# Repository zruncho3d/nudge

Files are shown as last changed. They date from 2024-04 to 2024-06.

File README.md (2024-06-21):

## Nudge - automatic nozzle alignment, made easy

*One microstep for a probe.  One giant leap for multiple-head-kind.*

**tl;dr:** Manual calibration sucks, but with this probe, you can get fresh, fully-automatic offset alignment on every print.

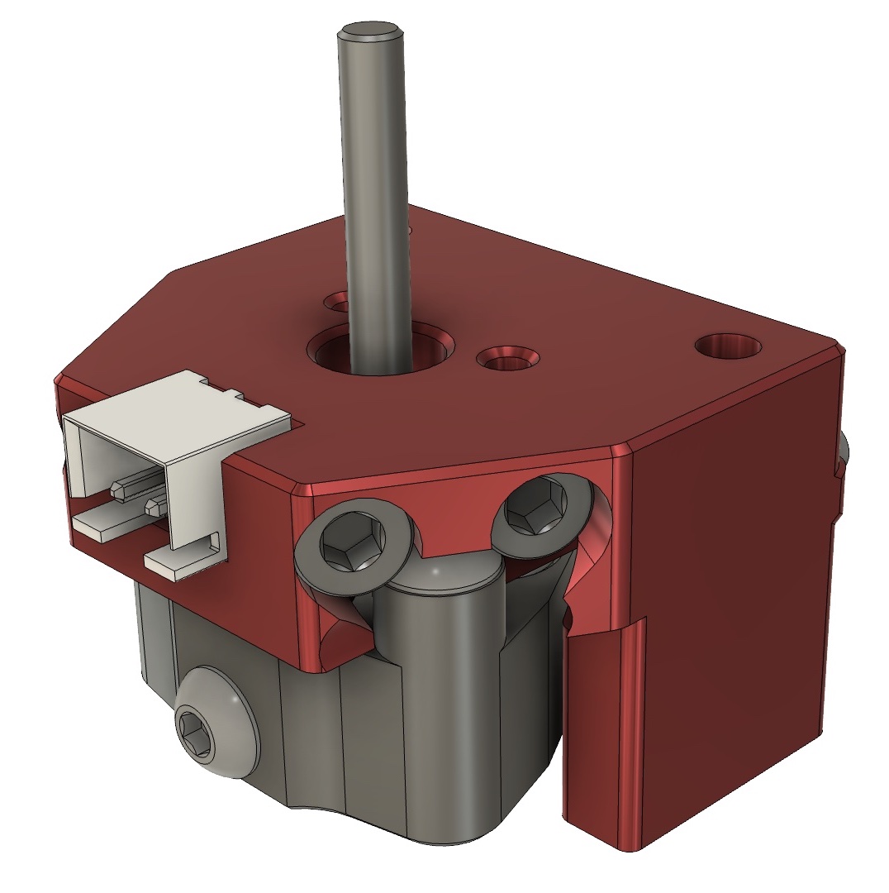
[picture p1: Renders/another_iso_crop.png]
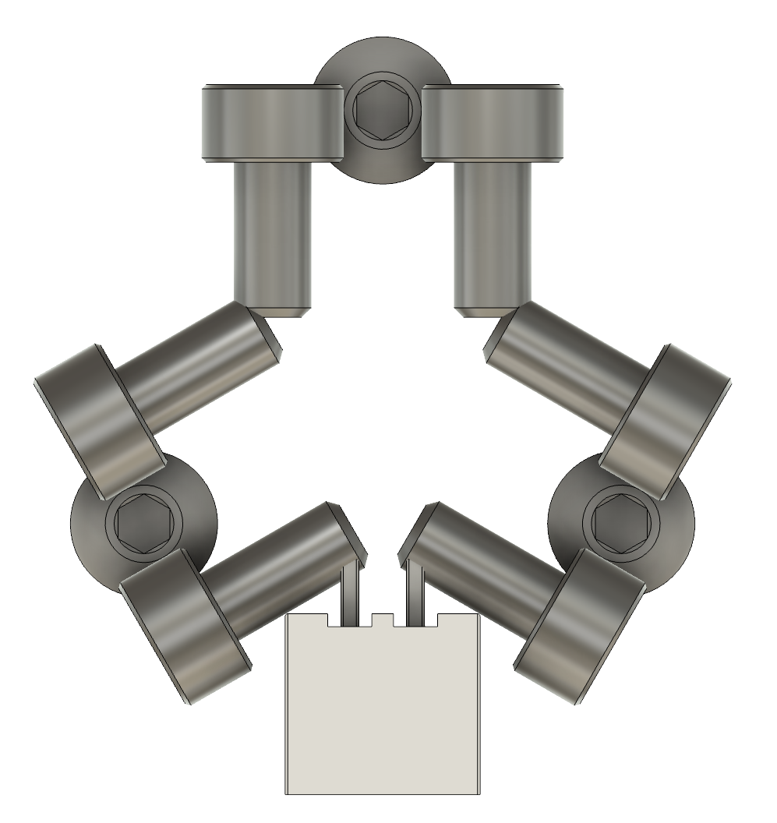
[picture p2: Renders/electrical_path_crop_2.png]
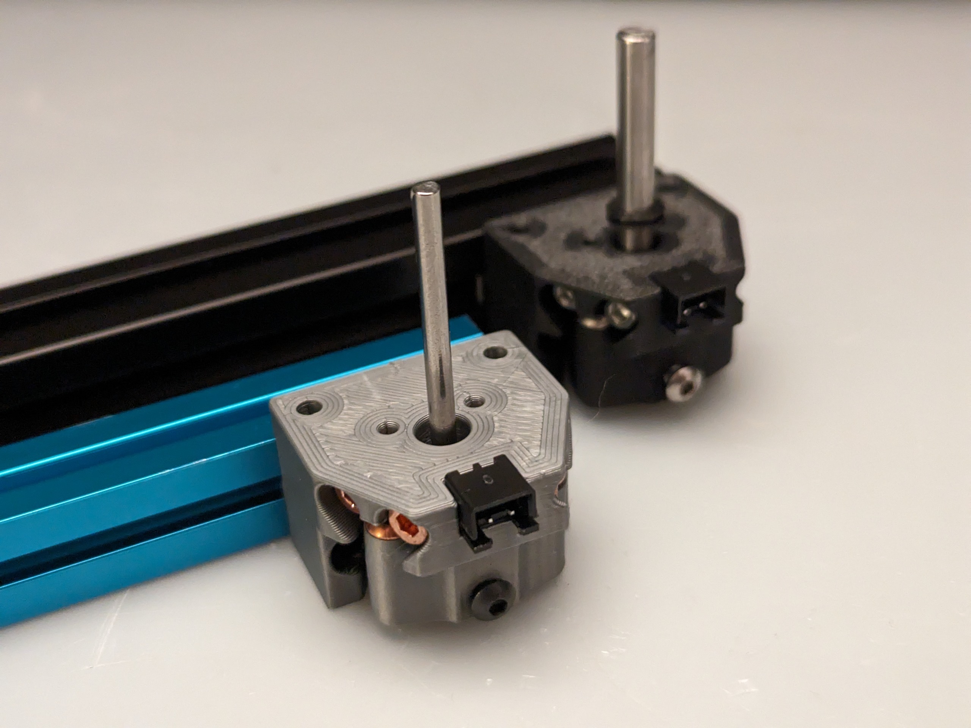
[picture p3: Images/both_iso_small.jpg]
|  |  |  |
| - | - | - |

## Nudge in action! >>>  

**Nudge** is a low-cost, high-repeatability probe to enable automatic nozzle alignment on multi-toolhead 3D printers (IDEX, Dual Gantry, and Toolchanger).  

It’s like a Z endstop, but can be nudged in X and Y directions, too.  

When the metal probe tip is nudged by the nozzle, a button-head screw in the Wobbler lifts off slightly from the smooth socket-head screws in the Mount, breaking the electrical path.  Software nudges the nozzle against the probe in Z, then X, and Y, repeating this process to determine offsets between any number of toolheads.

When multiple heads can work together, with perfect alignment, multi-color and multi-material prints look great!  

Here's a sample from Ankurv ([3DUnplugged]()), whose [Daksh v2]() toolchanger uses Nudge to ensure alignment betweeen heads:

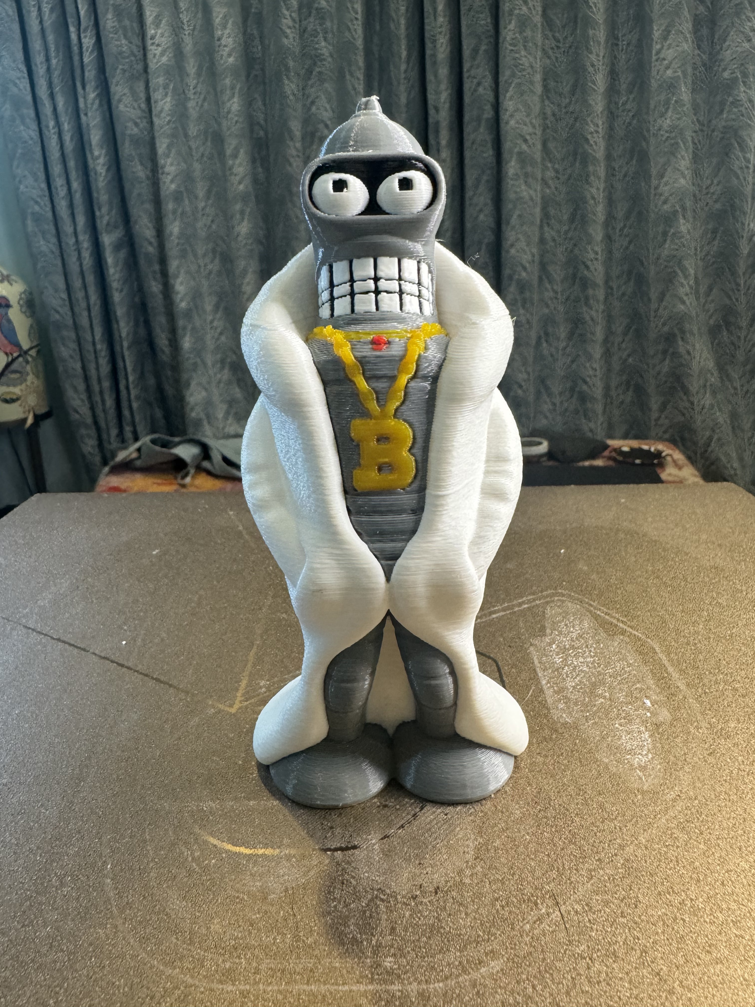
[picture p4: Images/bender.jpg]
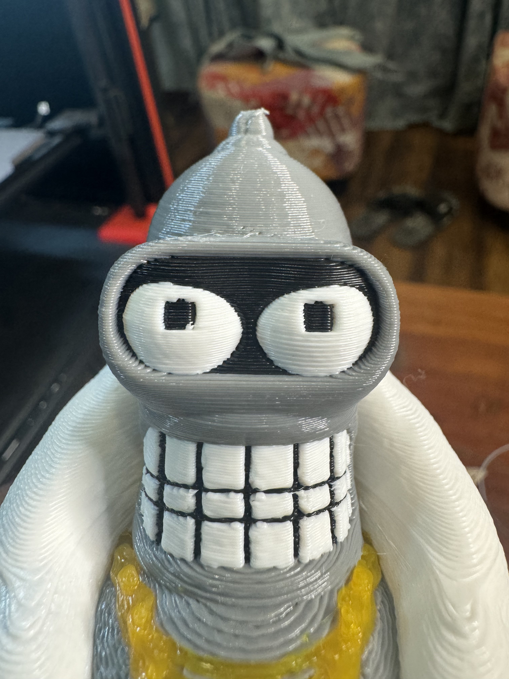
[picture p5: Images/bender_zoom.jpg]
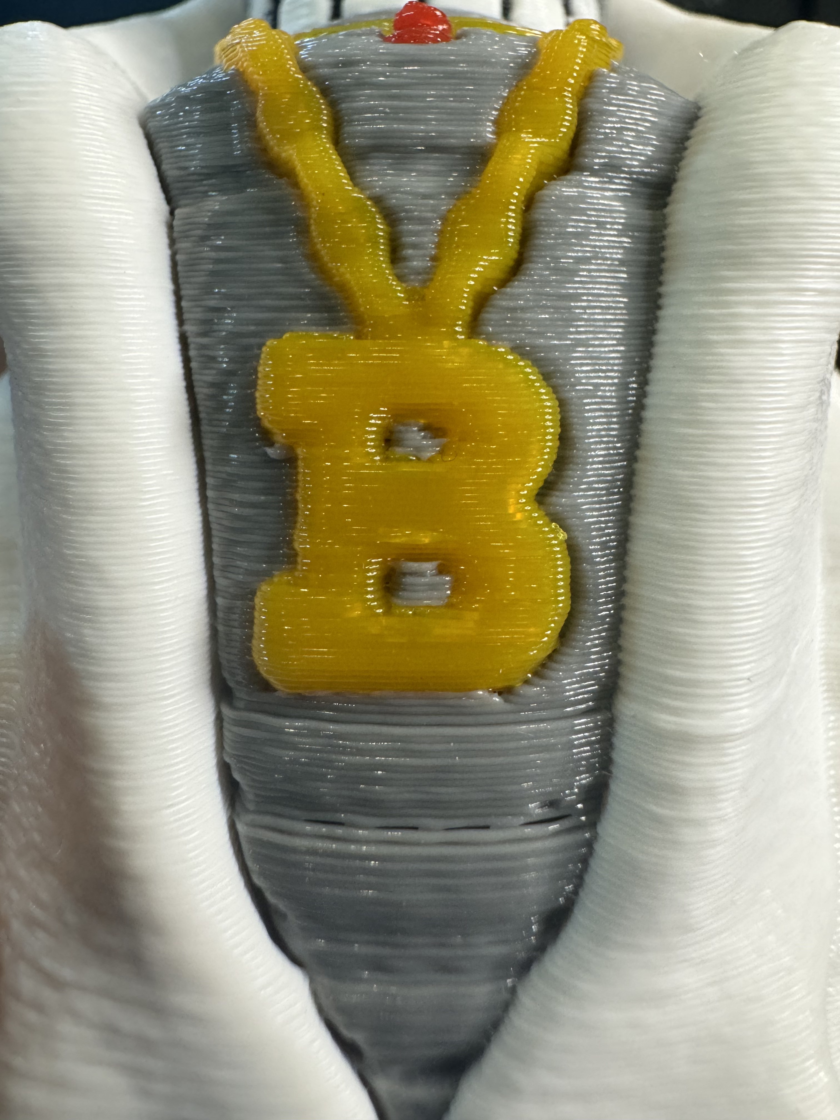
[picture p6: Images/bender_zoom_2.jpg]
|  |  |  |
| - | - | - |

Here's a sample from Zruncho of some Voron cubes.  The full-size cube would have been perfectly aligned if the nozzle was cleaned first!

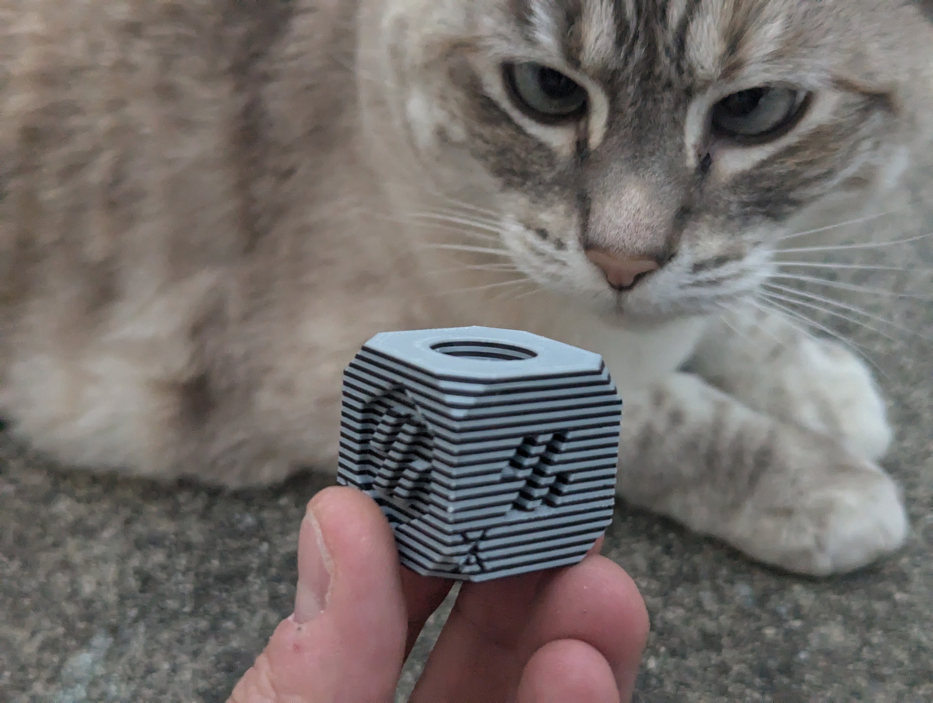
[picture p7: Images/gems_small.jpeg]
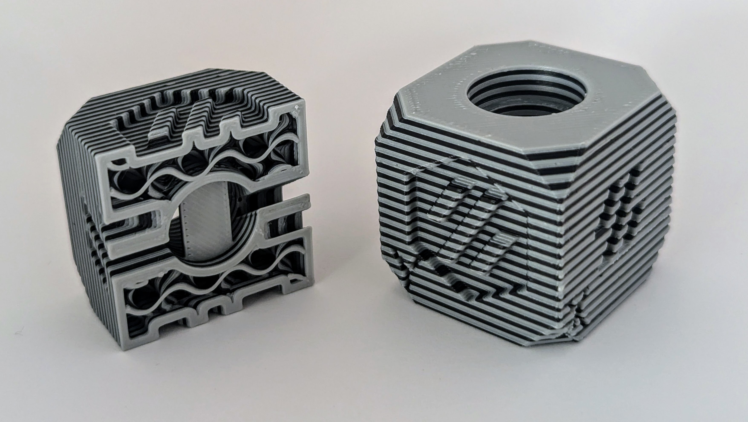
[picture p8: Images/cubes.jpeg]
|  |  |
| - | - |

You can print, build, and deploy a Nudge in as little as one hour, with only $10 in parts:

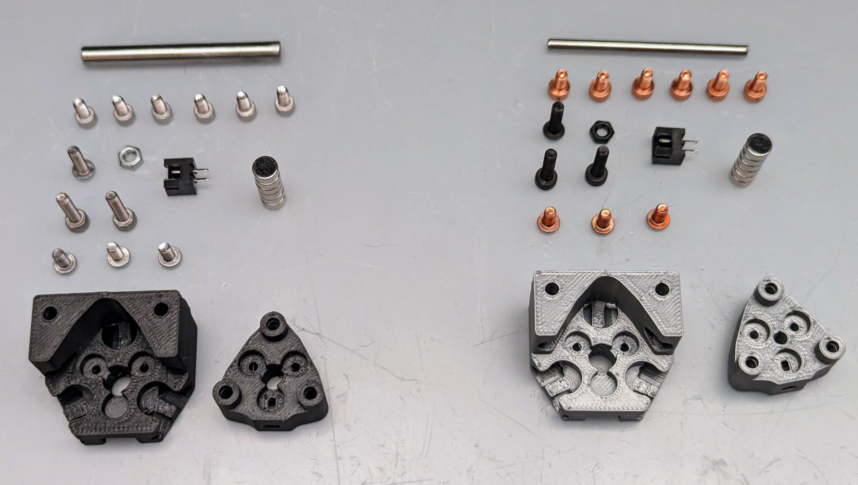
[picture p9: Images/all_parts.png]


Build it using the instructions in this repo, or with [this video]((https://youtu.be/6eRomxUo7TI).  Yes, it used to have a 'y' at the end of the name.  Note also that this video is slightly out of date - for example, now, Nudge has a straight-through JST, rather than a right-angle JST, and plastic to ensure the horizontal screws stay aligned.

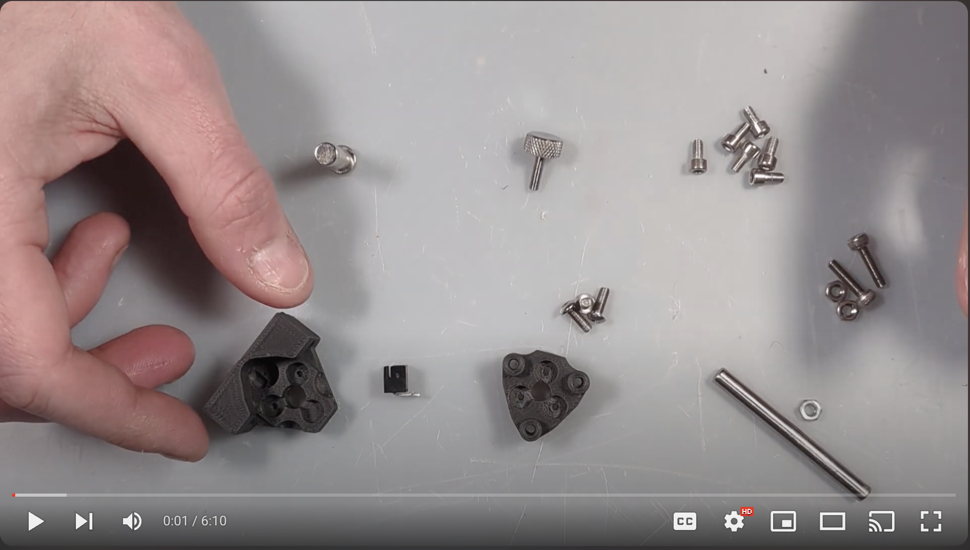
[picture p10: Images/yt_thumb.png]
(https://youtu.be/6eRomxUo7TI)


## [> > > Watch build](https://youtu.be/6eRomxUo7TI)

Nudge is highly repeatable; here's an early sample of probing accuracy from a 10-sample run:
```
Printing stats for x:
  Range: 0.0023
  Standard Deviation: 0.0010
Printing stats for y:
  Range: 0.0016
  Standard Deviation: 0.0007
--- 95.45 seconds total; 19.09 per iteration ---
```

Definitely usable!  Z is not quite as good, though, so you may still want to keep that endstop switch around for determining Z offsets.

**Firmware Support**: Nudge works great on CoreXY with nozzle alignment code from [Viesturz' klipper-toolchanger](https://github.com/viesturz/klipper-toolchanger) repo, but other kinematics should be possible with Klipper tweaks.

| Printer Type | Klipper Kinematics type | Test/Support Status |
| - | - | - |
| Toolchanger | CoreXY | :white_check_mark: |
| IDEX | Hybrid CoreXY w/ Dual Carriage | :white_check_mark: (as of 2024-06-19) |
| IDEX | CoreXZ Dual Carriage | :x: Fails during probing |
| DG | Dual Gantry CoreXY | :x: Fails during probing |

Related patches:
* [RCF's klipper-toolchanger fix for IDEX](https://github.com/viesturz/klipper-toolchanger/pull/23/commits)
* [Frans-Willem's Klipper PR for IDEX](https://github.com/Klipper3d/klipper/pull/6486)

No, fully-automatic offsets are not yet supported.  If you figure this out, please share.

**Hardware Support**: Mounting options for many common multi-toolhead open-source printers/mods are included here, including Trident, Tridex, Tri-Zero, Double Dragon, Dueling Zero, V2, Micron, F-Zero, and more.  One almost certainly fits!  *Unlike other options, a Nudge can be permanently mounted within a hot chamber, with as little as 6mm overtravel.*

**Parts to print**:

| Mount | Wobbler | Floating Base (optional) | Indexed Base (optional)  |
| - | - | - | - |
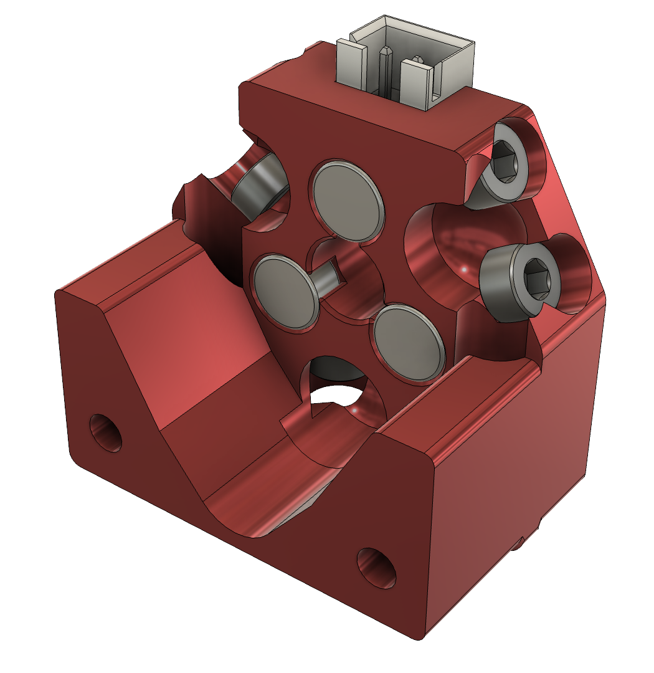
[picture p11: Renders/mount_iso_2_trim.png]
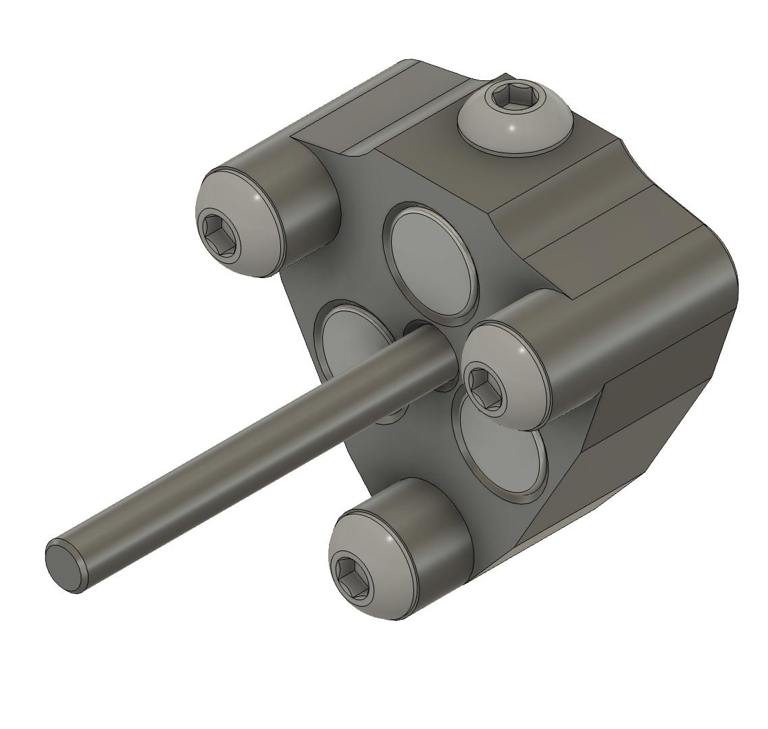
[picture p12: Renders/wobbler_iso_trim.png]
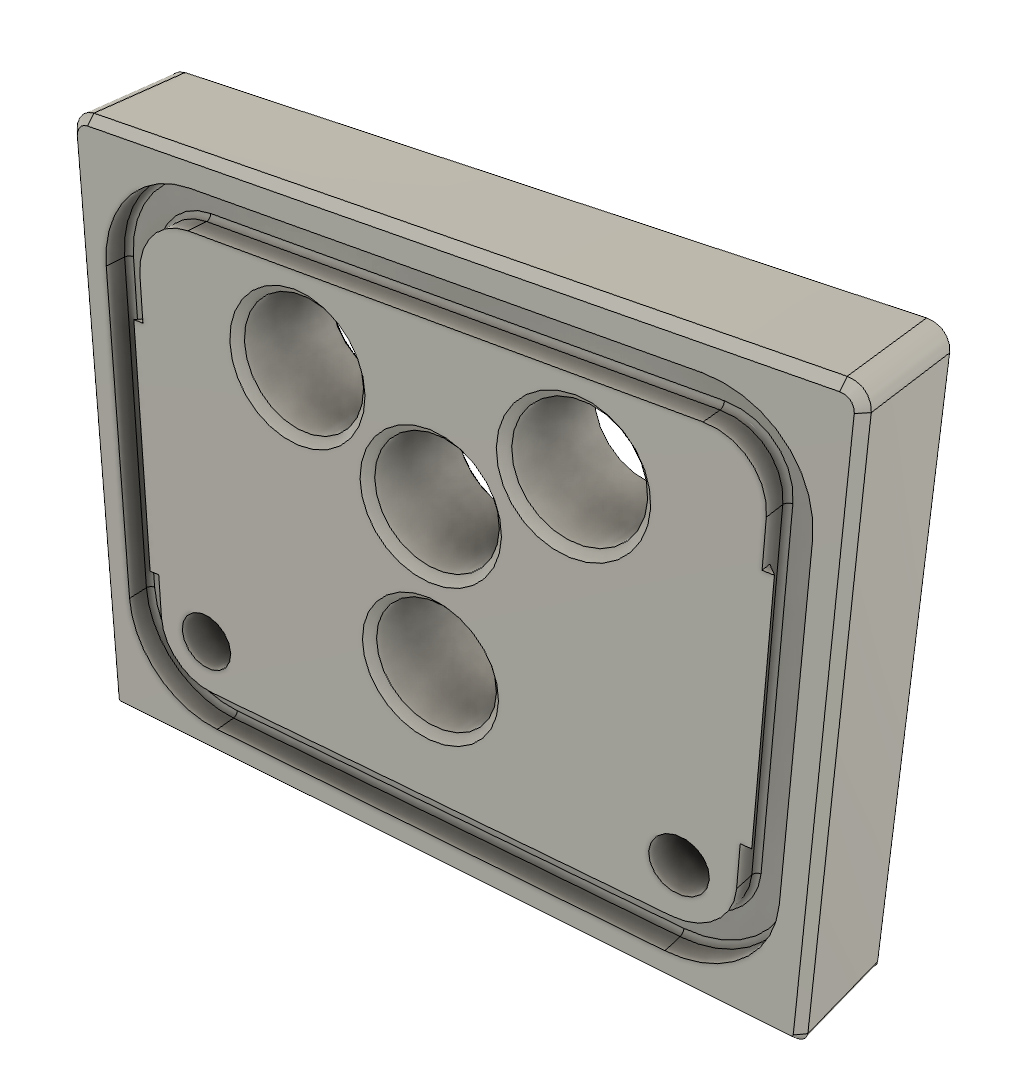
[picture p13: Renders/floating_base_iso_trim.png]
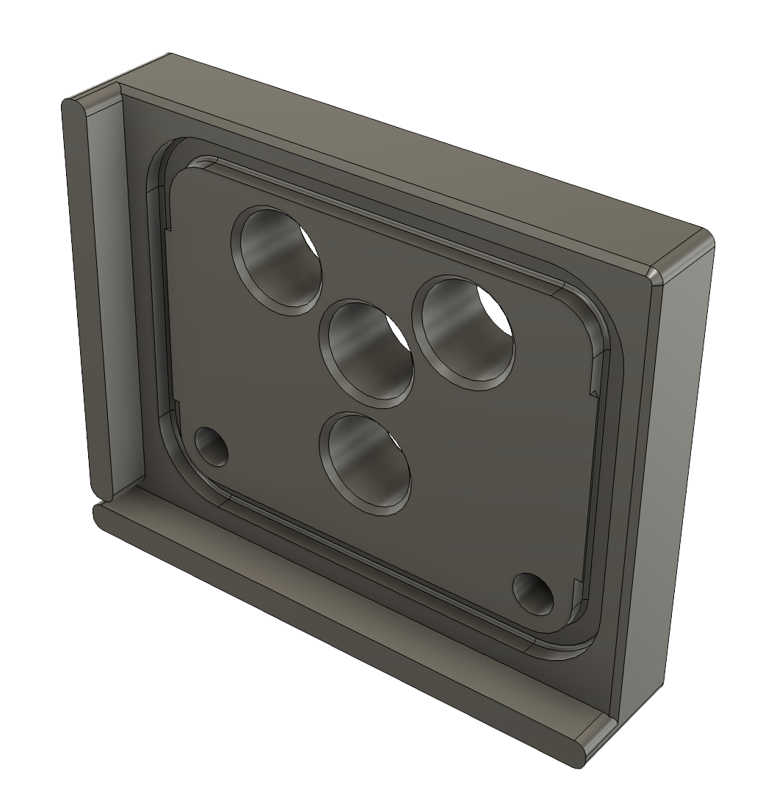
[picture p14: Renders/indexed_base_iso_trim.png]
|  |  |  |  |

**Mount options:**

| 2020 | 1515 High (sticks up) | 1515 Low (sits low) |
| --- | --- | --- |
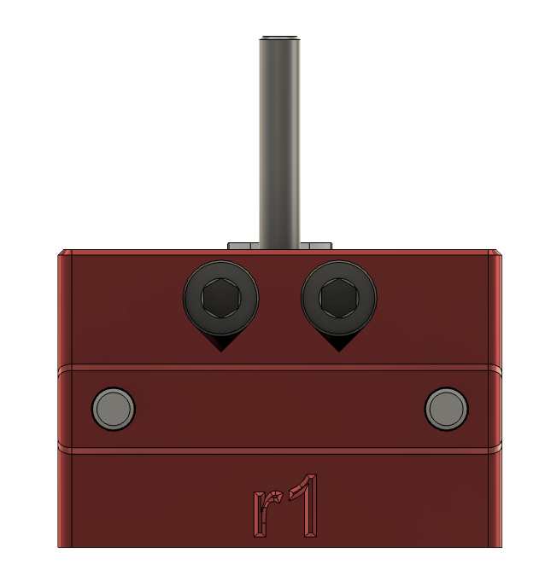
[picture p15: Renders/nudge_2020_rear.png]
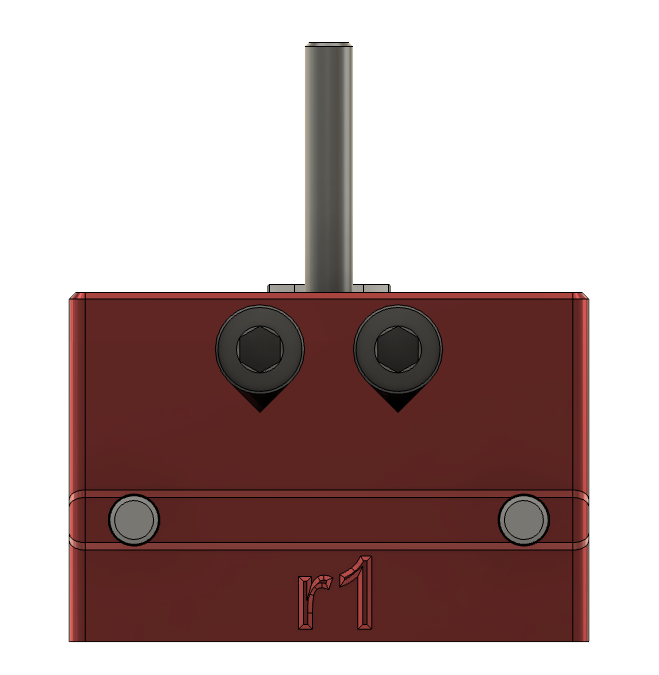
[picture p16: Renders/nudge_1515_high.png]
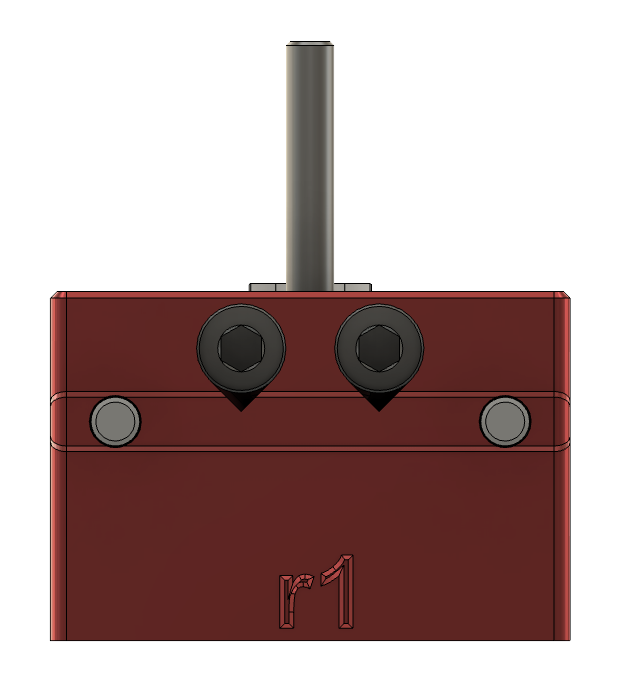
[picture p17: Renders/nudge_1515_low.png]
|  |   |  |

**Wobbler options**: 3mm Pin, 5mm Pin, or M3 screw and internally-threaded dowel:
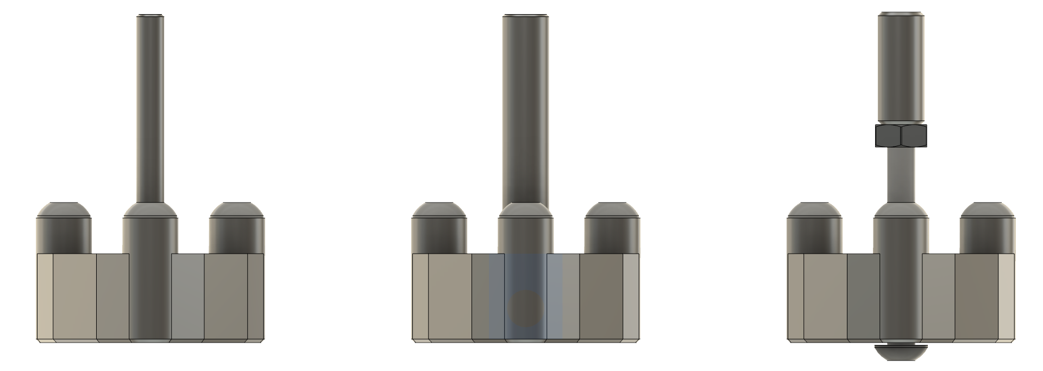
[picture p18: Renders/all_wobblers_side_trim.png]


**Sound good?**  Jump to the [Instructions](INSTRUCTIONS.md) section to get started and find the printed parts to match your printer's layout; one should fit!  

Or, read about some advantages to this design...
## Advantages
 * **Highly repeatable** - single-microstep-level repeatability (typically below .003125 Std Dev over 10 samples).
 * **Low cost** - approximately $10.
 * **Easily sourced** - Zruncho had all parts on hand already. All are on Amazon and AliExpress; smooth M3x6 SHCS is the only “new” part.
 * **Minimizes travel loss** - probe tip fits next to the bed; as little as 6mm overtravel suffices.
 * **Easily adjusted** - Z height, position along an extrusion, and magnet forces are all adjustable, in-situ.
 * **Fast build and print** - print, build, and test in about an hour.  No heatsets, soldering, or gluing required.
 * **Flexible mounting** - options are available to fit almost any printer.
 * **Simple wiring** - 2-pin JST header matches existing Z nozzle endstops.
 * **Temperature-tolerant** - no electronics to burn out at chamber temps (like a camera), and no plastic next to the bed to melt.
 * **In-place mounting option** - run this at the start of every print, just like a QGL or ZTA cycle, so that offsets are perfect, even with temperature changes, or after tightening or maintenance.

Like what you see?  [Buy me a coffee](https://ko-fi.com/zruncho3d) to show the love and enable future mods and content - stuff like [F0](https://github.com/zruncho3d/f-zero), [T0](https://github.com/zruncho3d/tri-zero), [B0](https://github.com/zruncho3d/boxzero), [X0](https://github.com/zruncho3d/double-dragon), [D0](https://github.com/zruncho3d/DuelingZero), [DX](https://github.com/zruncho3d/DuelingX), [ZeroPanels](https://github.com/zruncho3d/ZeroPanels), [ZeroClick](https://github.com/zruncho3d/zeroclick), [NoDropNuts](https://github.com/zruncho3d/f-zero/tree/main/STLs/NoDropNuts), [Poke](https://github.com/zruncho3d/poke), [Vampire Bat](https://github.com/zruncho3d/vampire_bat), and more.

 :heart: *-Zruncho*

## What's Here?

- #### [BOM](BOM.md): Parts list to build your own
- #### [Instructions](INSTRUCTIONS.md): Instructions to print and assemble
- #### [Configuration](CONFIGURATION.md): Configuration - firmware & macros
- #### [Design](DESIGN.md): Learn about why Nudge is designed like that!
- #### [FAQ](FAQ.md): Common questions, answered

## Troubleshooting

**Probe not returning to center?** Magnet force may be insufficient, especially with heavier 5mm pins.  You can easily increase magnet force by cutting the screw towers and aligning the BHCSes to decrease magnet distance.  You can also just push the magnets out slightly for the same effect.  Worst-case use stronger magnets.

**Probe triggered early?** Increase `spread`, improve the initial alignment accuracy, or add travel (by moving the bed or sensor).

**Probe triggering unreliably?** Check each pair of screws with a multimeter.  After a few heat cycles, you will probably need to tighten the SHCSes, as the plastic likes to relax a bit.

**High result variation?** Check the rigidity of the mount and be absolutely sure

**Unsatisfied with Z repeatability?** Z is just not as good, due to the design.  You can keep your original endstop and wire it inline with the original Z endstop, or you can flip the Nudge upside down and change the config to use Tap/Boop etc for the Z probing.

## Support

Find the thread in the User Projects forum channel on the [DoomCube Discord](https://discord.gg/doomcube) and post there.

## Credits

**Enjoy!** I hope you enjoy using this as much as the beta team did bringing this to release!  

Special thanks to `Caza` for critical design feedback and ideas, `Ankurv` for all-up testing,  and the beta team who helped validate the design: `Telxoid`, `Esoterical`, `SteveBuilds`, and others who provided data and feedback, including `RCF` and `Frans-Willem`, who created a PRs for IDEX.

We made a lot of prototypes and test articles to get here.

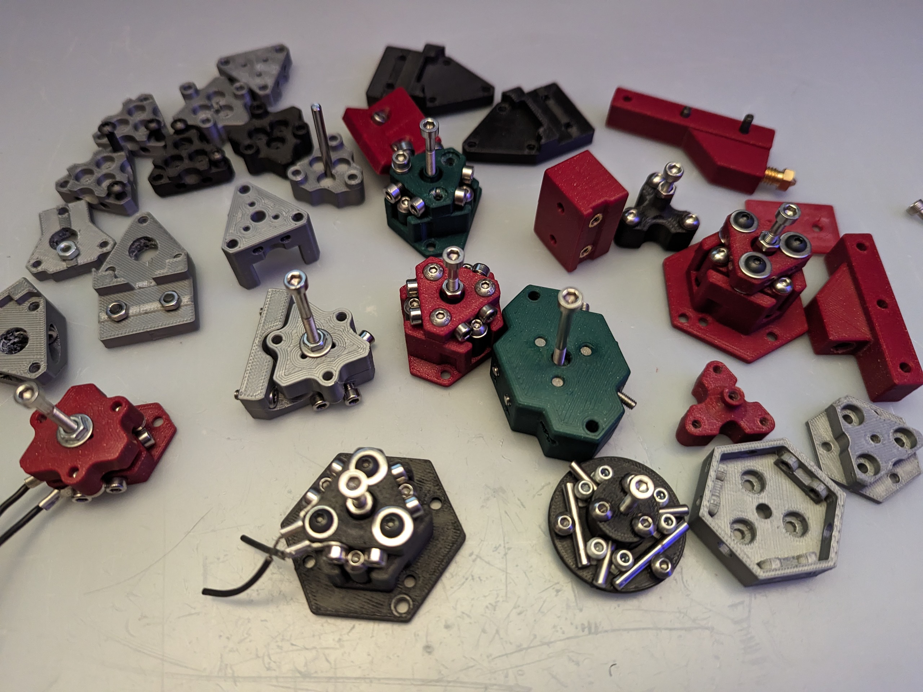
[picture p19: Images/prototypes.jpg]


It's 60+ and this isn't even all of them.

Thanks also to [Fabreeko](https://www.fabreeko.com/) for supporting this build!  Without HoneyBadger rails, the test gantry would not have happened, and Nudge would not have been as good.  Support vendors like this, which support open-source dev, whenever you can.

-Z

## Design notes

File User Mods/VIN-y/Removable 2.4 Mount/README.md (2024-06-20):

# About

This mod prove a repeatable mounting point for the stock Nudge near the back right corner of the 2.4 bed.

### Feature:

* Avoid reducing built volume in the Y-axis.

* Provide docking point for the Nudge, when not in usage.

* Feature a safety switch, that is triggered and prevent attempts to calibrate if the nudge is still docked.

### BOM:

* 3mm X 20mm pin (2 off)

* 6mm X 3mm, Neodymium Magnet (3 off)

* 3mm Bore x 5mm OD x 5mm Length Plain Bearings (6 off)

* Micro switch (1 off)

* 2mm self-tapping screws (2 off)

* M3 x 20mm (2 off)

* M3 x 18mm (1 off)

* M3 x 5 x 4 threaded insert (1 off)

* M3 washer (1 off)

* M3 x 25mm counter sunk (2 off)

* Super glue - for the magnets (optional)

### Notes:

* As the 3mm pins and sleeves are press-in-place, you might need a parallel clamp that can open at least 32mm wide. Alternatively, you can widen the holes with 3mm and 5mm drill bits.

* BE MINDFUL OF THE MAGNET DIRECTION. The part will need to be destroyed for magnet recovery.

### Pictures:

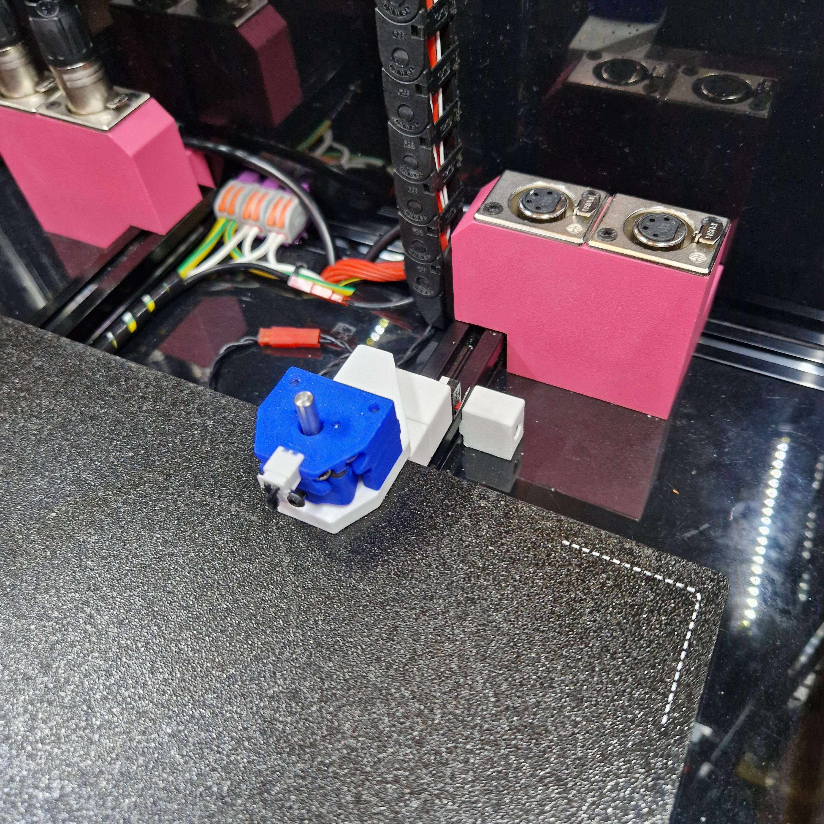
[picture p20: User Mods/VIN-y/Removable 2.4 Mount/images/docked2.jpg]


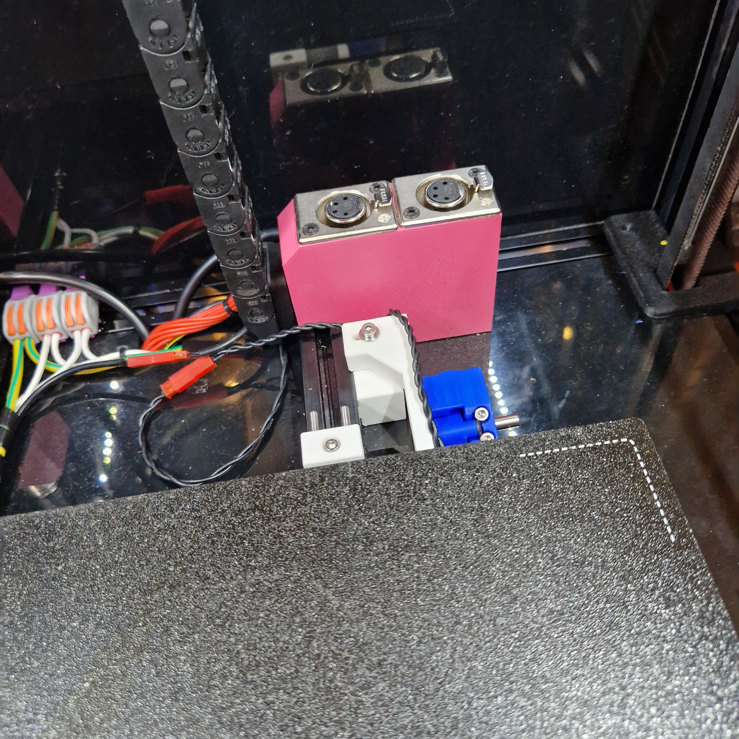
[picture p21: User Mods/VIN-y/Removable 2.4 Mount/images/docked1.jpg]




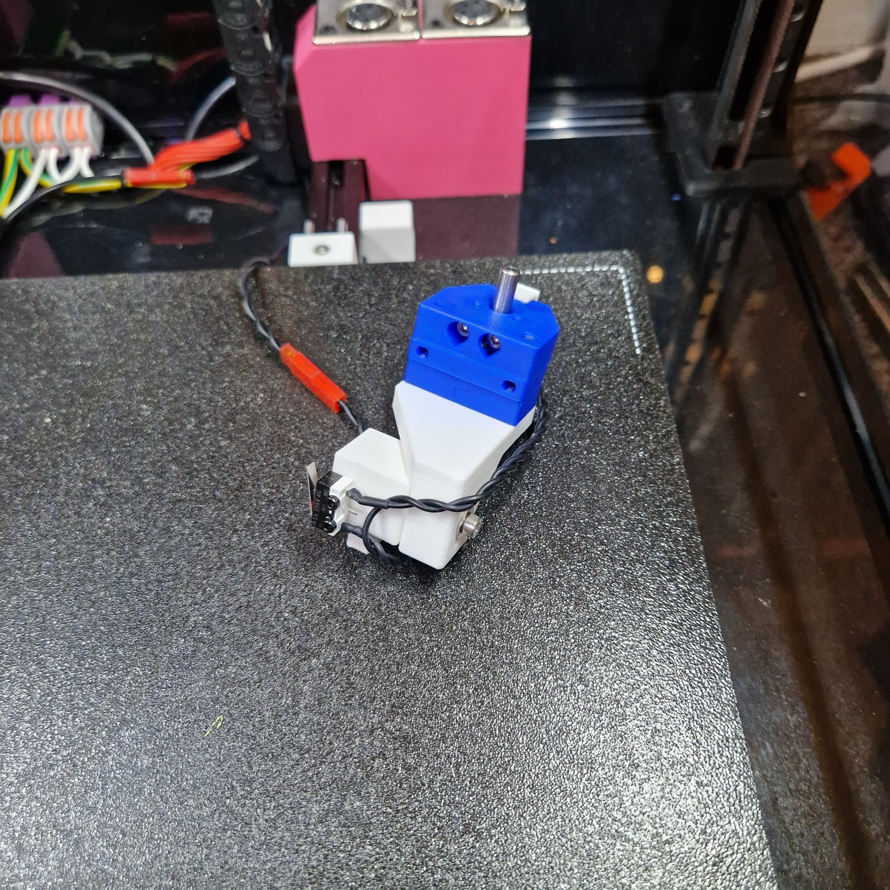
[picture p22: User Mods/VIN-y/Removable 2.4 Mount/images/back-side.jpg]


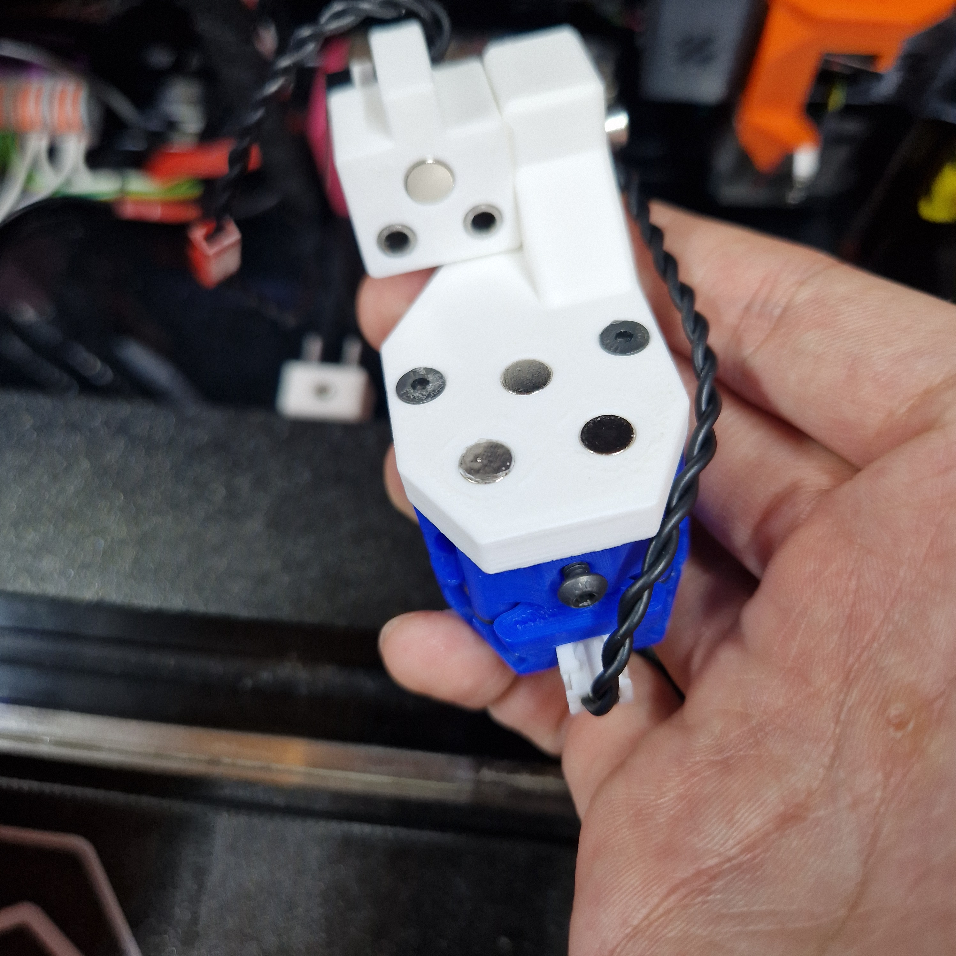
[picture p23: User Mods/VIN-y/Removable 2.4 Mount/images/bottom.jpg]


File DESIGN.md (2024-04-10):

# Design

**What’s interesting here?**

There's a lot of design complexity in a tiny space.  This is a 100% functionality-optimized design.

The key is the electrical layout.

In Nudge, M3 socket-head screws serve triple-duty as (1) NC (normally-closed) electrical contacts, (2) Maxwell-type kinematic couplings, and (3) contacts for the external (JST) connection.  Let's unpack that.

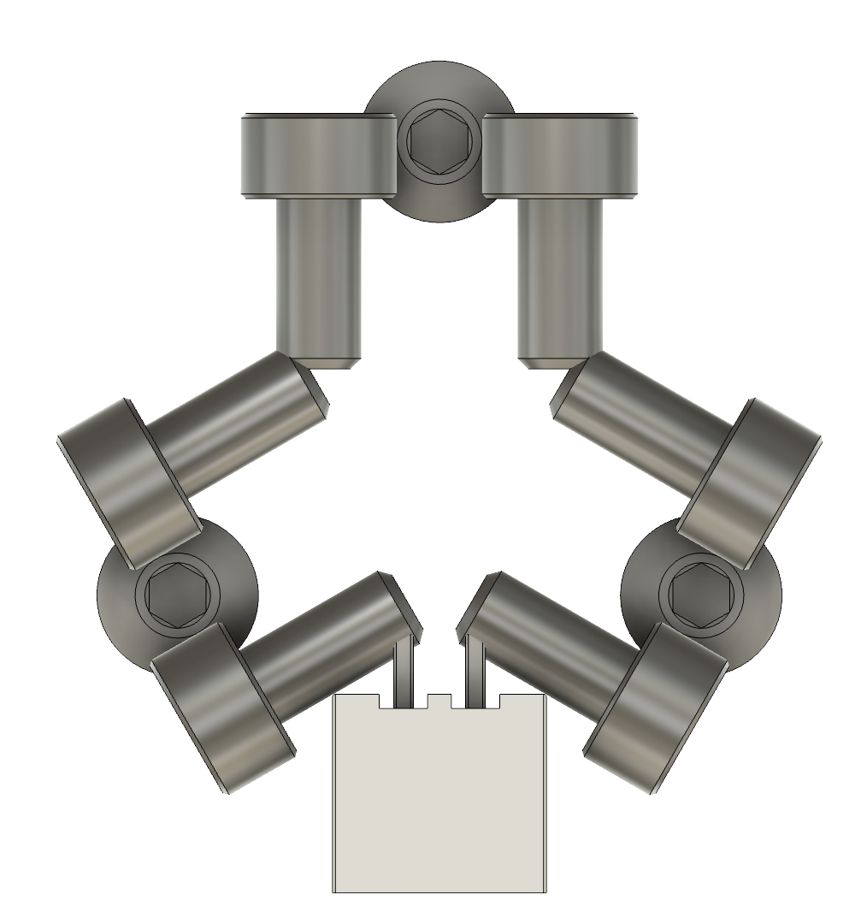
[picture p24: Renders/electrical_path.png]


**Electrical Contacts**: the cylindrical surface of the socket-head screws interacts smoothly with M3 button-head screws and forms a good electrical contact when pushed together with enough force.  Basic N35 6mm magnets work well here; in tests, this setup proved more repeatable than springs, without requiring any force tuning.  You can still tune the attraction between the mount and the wobbler, by unscrewing the wobbler screws evenly.  Stronger magnets required too much probe force, which measurably stretched the belts during long repeatability tests.

The screw tips press into each other, closing electrical contacts; this choice eliminated the need for more parts.  Originally, the screws faced out and used carefully bent solid wires or ring/spade terminals with flexible wire.  Screws facing in is much better.   Thanks `caza` for that suggestion!

Putting both parts of the SHCS to work required designing around specific screw lengths, and getting it all to work with tiny M3x6 screws was a challenge.

**Maxwell-type Kinematic Coupling**: A Maxwell coupling is a type of kinematic (repeatable) coupling that is symmetric.  The whole setup is similar to a Renishaw-style touch probe for CNC.

**Contacts for external JST connections**: the screw cuts a thread against the square JST terminals to close the connection.  The design evolved from ring terminals clamped by the screws (extra parts to source), to direct wire clamps, to a vertically-pointed straight JST, to a right-angle JST, to finally, a front-facing straight-through JST.  If people have issues with the cut screws, we can always revert to right-angle terminals.

**Design for Printability**:
A lot of thought/work went into designing this for clean 3D printing:
* overhangs beyond 45 degrees are avoided: teardrops around the rear-most two screw holes are an example
* careful multi-stage bridging near the JST connector
* the STls are oriented with seams at back

**Design for Assembly**:
* The shrouds around the SHCS guide screw in; without these features, the SHCS can go in slightly crooked.
* Magnet removal holes help when you have bajillions of prototypes
* Magnet holes are aligned to perimeters to enable press-fit magnets
* All formed threads have small counterbores to hold the screws ("easy starts)"
* The bases have little grips for the filament or o-ring.
* An earlier version required a separated mount and core, but these made sense to integrate, and Nudge became more compact and faster to assemble.
* Out of all the probe targets tried, pins were the fastest to assemble in the field, especially when combined with a locking screw.

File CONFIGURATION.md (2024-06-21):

# Configuration

Instructions below assume Klipper.  If you use RepRapFirmware or another firmware, PRs are welcome.

#### Add klipper-toolchanger code to Klipper

Formerly called NozzleAlign, the `tools_calibrate` code by Viesturz in the `klipper-toolchanger` repo finds the center of the probe, as well as computes the XYZ offsets relative to a different probing run.  CoreXY toolchangers have always been supported, and as of 2024-06-19 and a [patch by RCF](https://github.com/viesturz/klipper-toolchanger/pull/23/commits), IDEX support is merged into the mainline.

This code plunges to find the Z position, then moves in +X, -X, then -Y, +Y directions, with a Z offset you select.

These instructions come from Viersturz’ [klipper-toolchanger](https://github.com/viesturz/klipper-toolchanger) repo.

First, SSH to your Klipper system, then install the klipper-toolchanger code:
```
wget -O - https://raw.githubusercontent.com/viesturz/klipper-toolchanger/main/install.sh | bash
```
Klipper should restart without issue.

As best practice, enable easy updates: add this chunk to Moonraker.conf and restart Klipper when prompted:
```
[update_manager klipper-toolchanger]
type: git_repo
channel: dev
path: ~/klipper-toolchanger
origin: https://github.com/viesturz/klipper-toolchanger.git
managed_services: klipper
primary_branch: main
install_script: install.sh
```

#### Add recommended Klipper config

* Set 64x microstepping in X and Y with typical 20t pulleys and 200 steps/rev motors
  * Means 0.003125mm step

#### Add NozzleAlign config

Add the `calibrate_offsets.cfg` sample below, read the comments, and make sure your pin name and travel are set to match your deployment.

```
[tools_calibrate]
# Nudge config
#
# These two values should be changed or checked.
#
# 'pin' should reference the pin used for Nudge.
pin: z:PC0
# 'spread' is the amount of X or Y motion used in the probing sequence.
# Think of it as the clearance from the center, to accomodate the pin's diameter and any
# initial starting-point inaccuracy.
# For larger pins (5mm), increase this to 3.5mm+.
#   Increase this and/or improve the accuracy of the starting point if the probe triggers too early.
#   Decrease this and/or improve the accuracy of the starting point if the motion
#     pushes your printer beyond the allowed travel amount.
spread: 3
#
# Config below is unlikely to need changes.
#
# 'lower_z' is the distance below the probe tip in Z, used to ensure a hit.
#   Increase this to have more of the nozzle hit during probing.
#   Values as low as 0.1mm may work, and will minimize the need for overtravel.
lower_z: 0.2
travel_speed: 100
speed: 2.5
lift_speed: 4
final_lift_z: 4
sample_retract_dist: 2
samples_tolerance: 0.05
samples: 1
samples_result: median
trigger_to_bottom_z: 3
# If using a built-in Z probe to find the Nudge pin top, reference it here.
# This is only relevant for the flipped configuration, to provide resistance to pushing, for Tap/Boop/Poke/etc.
# Most should leave this commented out.
#probe: probe
```

Reference this added `calibrate_offsets.cfg` file in your printer.cfg:

```
[include calibrate_offsets.cfg]
```

Note that this include must come after the `[probe]` section.

Restart Klipper via Mainsail.

Confirm installation, and that config is in the right place, by typing `TOOL_` and seeing that `TOOL_LOCATE_SENSOR` appears.

#### Maximize and confirm travel

Maximize overtravel first: adjust the X or Y endstop, or adjust the endstop position in config.

The examples below assume a rear-mount Nudge on a 300mm-bed printer; adjust as needed.

```
G28
G0 X150 Y300
```

Ensure that the nozzle has at least 1mm clearance to the edge of the pin.  

#### Find center of probe

You don’t have to be exact as you can put in the precise center after the first iteration.

Do your best, visually, to align to the center of the probe.

#### Set up Klipper macros

The examples below derive from Viesturz' repo.

Copy the macros below, updating the X and Y positions in `NUDGE_MOVE_OVER_PROBE`, and matching your number of tools.
```
[gcode_macro NUDGE_MOVE_OVER_PROBE]
gcode:
  G0 Z3
  # Put your specific values here!
  # Update them too, after the first run.
  G0 X175 F9000
  G0 Y304 F9000

[gcode_macro NUDGE_FIND_TOOL_OFFSET]
gcode:
  NUDGE_MOVE_OVER_PROBE
  TOOL_LOCATE_SENSOR

[gcode_macro NUDGE_FIND_TOOL_OFFSETS]
gcode:
    T0
    M109 T0 S150  # Heat up as much as possible without oozing to account for any thermal deformations
    NUDGE_FIND_TOOL_OFFSET
    M104 T0 S0
    # Match your number of tools:
    #   [1, 2, 3] for a 4-head toolchanger.
    #   [1] for IDEX or Dual Gantry.
    {% for tool in [1] %}
        T{tool}
        M109 T{tool} S150
        NUDGE_MOVE_OVER_PROBE
        TOOL_CALIBRATE_TOOL_OFFSET
        M104 T{tool} S0
    {% endfor %}
```

Save and restart.  

#### Do a Nudge probe

Do it:
```
G28
NUDGE_FIND_TOOL_OFFSET
```

A valid run looks like this in the Klipper console:

```
17:46:22
Sensor location at 25.061719,121.396875,2.337500
17:46:22
Probe made contact at 25.060156,124.133594,1.837500
17:46:18
...
...
...
Probe made contact at 22.360937,121.500000,1.882500
17:45:54
Probe made contact at 25.000000,121.500000,2.382500
17:45:53
TOOL_LOCATE_SENSOR
17:45:43
GO_TO_PROBE
```

Run it a few times in a row; the detected center values should be very close - within a microstep.

#### Get offsets via Nudge

Now, you should be able to automatically have this all work:

```
NUDGE_FIND_TOOL_OFFSETS
```

Note the output at the end, which shows offsets.  

Recommended: run this a few times; any variation beyond 0.01-0.02mm in X or Y suggests that the nozzle could use cleaning, or the mount is insufficiently rigid.

A bunch of probing to break it in can't hurt, either.

Copy the offset values you see into the configuration for each head.

####  Clean your nozzles

Dried crud will definitely show in your measurements, and possibly cause them to fail.

Hot crud will mess up the measurements too.

You want a clean nozzle for good results.

#### Center-finding repeatability

You can run `printer-experiments` on your laptop for max convenience, or run it on a Pi itself too.
* Clone the [printer-experiments](https://github.com/zruncho3d/printer-experiments) repo
* Install the python deps, so you can do `python3 run_test.py -h` and see help text.  Look for `pip3` in the code and run that on the command line.

Create a simple script like `test_tool_locate_sensor.sh` with content like this:
```
#!/usr/bin/env bash
# Param 1: number of reps
# Param 2: suffix for file to write
python3 ./run_test.py gantry.local \
--test_type tool_locate_sensor \
--start_gcodes '["G28", "NUDGE_MOVE_OVER_PROBE"]' \
--iterations $1 \
--stats \
--data_keys xyz
#\
#  --output \
#  --output_path myprintername/2023-12-23-x_positions_${1}_${2}.json
```

Run the script, and watch as it prints out glorious data.  The parameter (`$1` in bash) is the number of iterations.   For example, for 3 iterations: `bash test_tool_locate_sensor.sh 3`.

At the end of the run, the script will print out ranges and Std Devs for each specified `data_key` axis (here, `x`, `y`, and `z`).  Sample output from `Telxoid` showing something interesting:

```
Printing stats for x:
  Range: 0.0219
  Min: 100.6094
  Max: 100.6312
  Median: 100.6188
  Standard Deviation: 0.0049
Printing stats for y:
  Range: 0.0844
  Min: 251.0781
  Max: 251.1625
  Median: 251.1203
  Standard Deviation: 0.0228
```

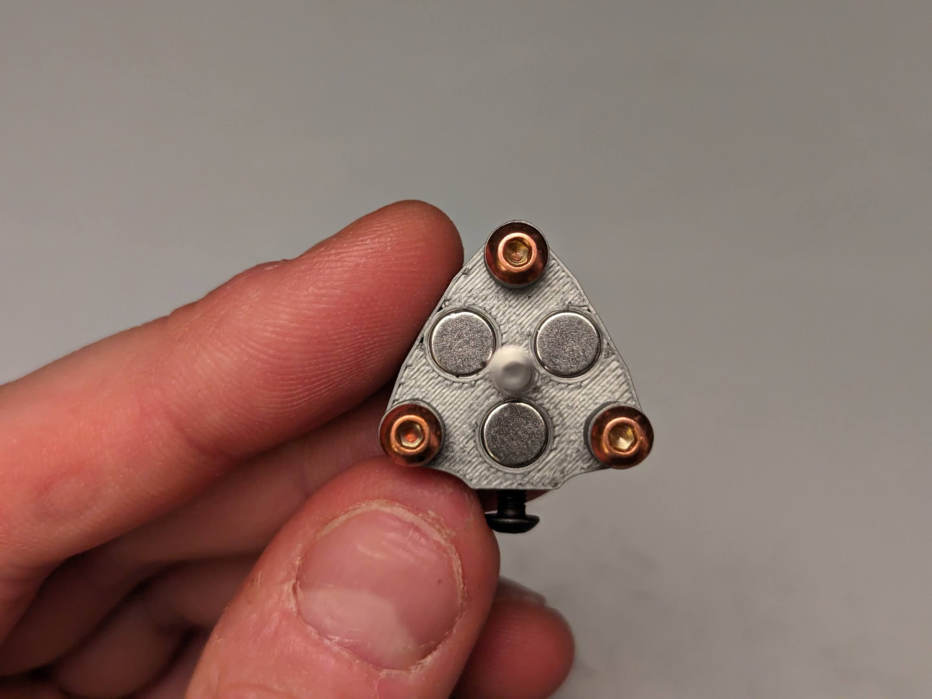
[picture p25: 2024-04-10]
Images/silver_wobbler.png

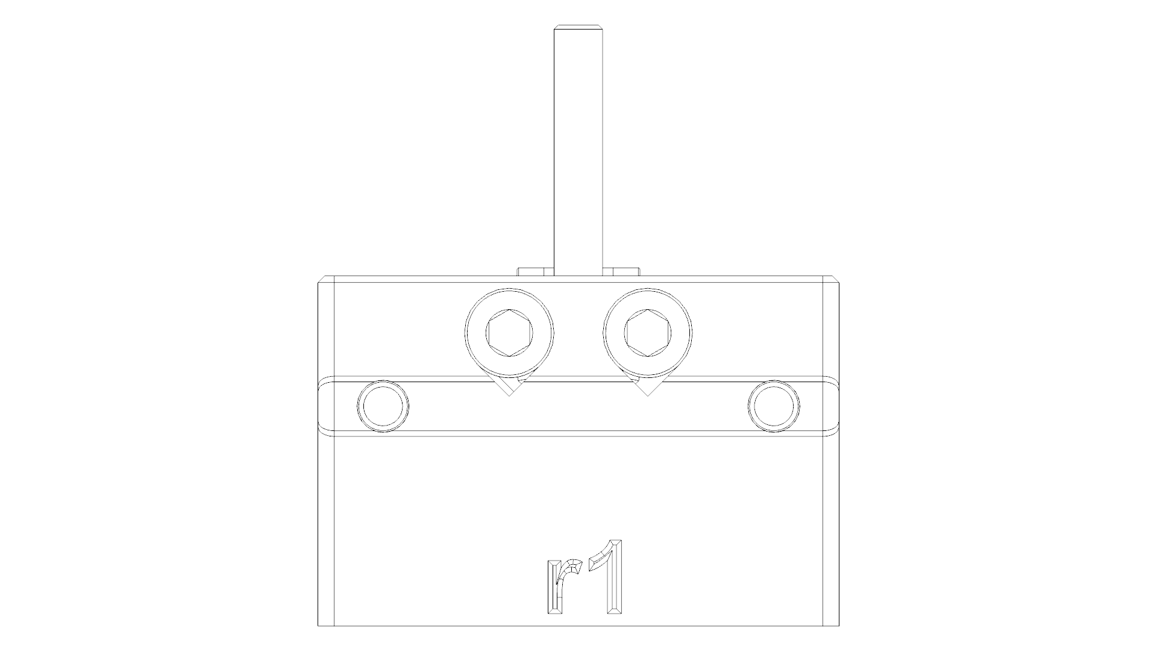
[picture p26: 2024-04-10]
Renders/1515_low_rear_wireframe.png

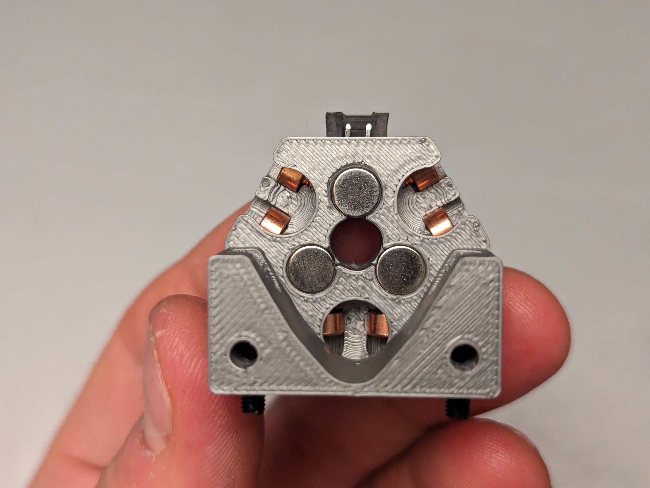
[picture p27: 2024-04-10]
Images/silver_bottom.png

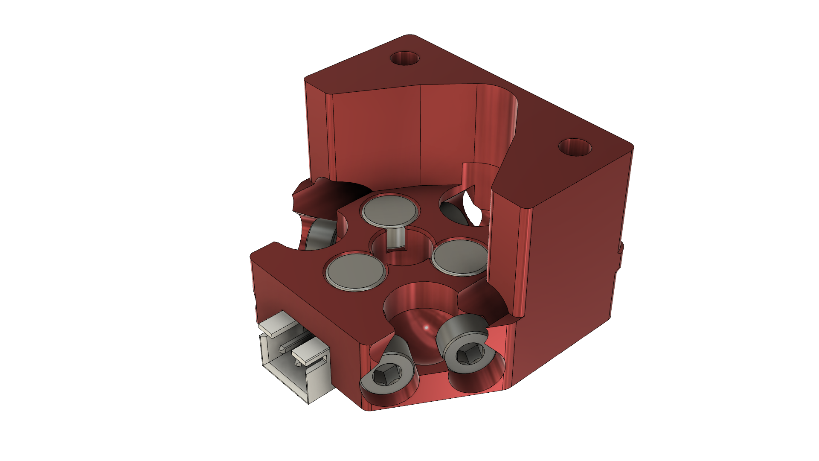
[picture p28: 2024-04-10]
Renders/mount_iso.png

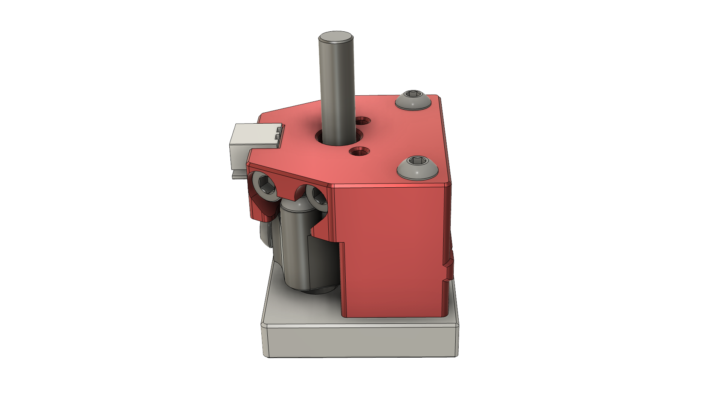
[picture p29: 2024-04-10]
Renders/nudge_with_floating_base.png

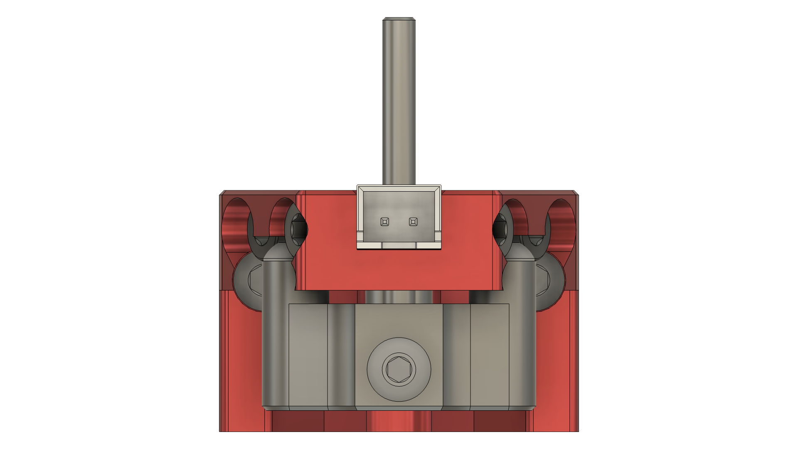
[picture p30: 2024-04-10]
Renders/front_view.png

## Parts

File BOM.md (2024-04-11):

# Bill of Materials

* Probe Target
 * 1x 5mm or 3mm pin: length depends on your setup (30mm-5mm typically)
 * 1x Locking Screw: M3x10 BHCS/SHCS/thumbscrew
 * 1x M3 nut
* Magnets
 * 6x 6mm x 3mm magnets - must be basic N35, **NOT N52**; [Amazon](https://www.amazon.com/gp/product/B077K364Z7/ref=ppx_yo_dt_b_search_asin_image?ie=UTF8&psc=1)
* Mounting Screws
 * Mount on extrusion: 2x M3x12 SHCS
 * Floating and indexed bases: 2x M3x25 BHCS
* Main Screws
 * 6x M3x6 SHCS
   * **MUST BE SMOOTH HEAD**; no knurling allowed.
   * **MUST BE CONDUCTIVE**; no black oxide or anodized ones here.
   * Copper is recommended: [AliExpress](https://www.aliexpress.us/item/3256804060768619.html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), but stainless is OK in practice: [Amazon](https://www.amazon.com/dp/B0895NYSBT?ref_=cm_sw_r_cp_ud_dp_M44EYYXNMSRJQ80XQM60&peakEvent=4&dealEvent=1&th=1), [McMaster-Carr](https://www.mcmaster.com/90035A110/)
* Midpiece screws
 * 3x M3x6 BHCS
   * **MUST BE CONDUCTIVE**; no black oxide or anodized ones here.
   * Copper preferred [AliExpress](https://www.aliexpress.us/item/3256805885958581.html), but stainless is OK in practice.
* Connector
  * 1x straight 2-pin JST-XH male connector, + matching crimps and housing
* Floating and indexed bases only:
  * 1.75mm TPU or equivalent-size O-ring or similar-size rubber band
  * Up to 8x additional 6mm magnets for base (can be N52), can be double-stacked
* OPTIONAL Super Glue for magnets; shouldn’t be needed if the fit is right.

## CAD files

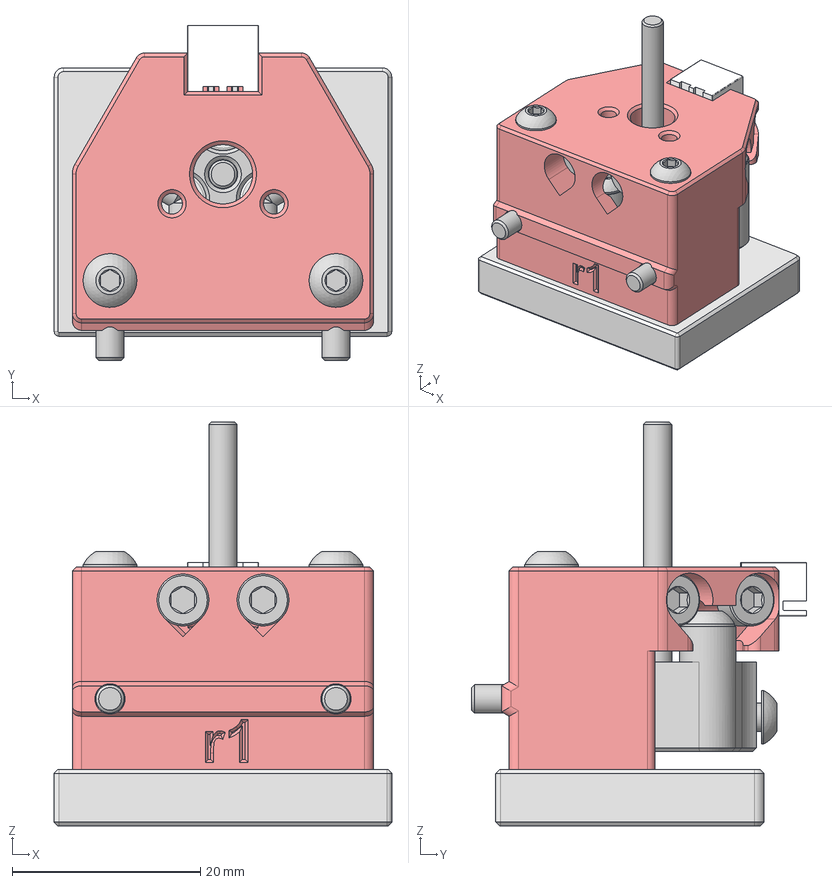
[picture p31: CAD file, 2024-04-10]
CAD/Nudge_1515_High_3mm.step
35.8 x 35.6 x 42.9 mm
M3x6 SHCS x 6
6x3mm Magnet x 6
Floating Base
M3x25 BHCS v1 x 2
Adjustable Dowel
SHCS
m3_pin_main 35mm
M3_Hexnut
M3x10 BHCS v1
M3x6 BHCS v1 x 3
XH2.54-2P
M3x12 SHCS v1 x 2

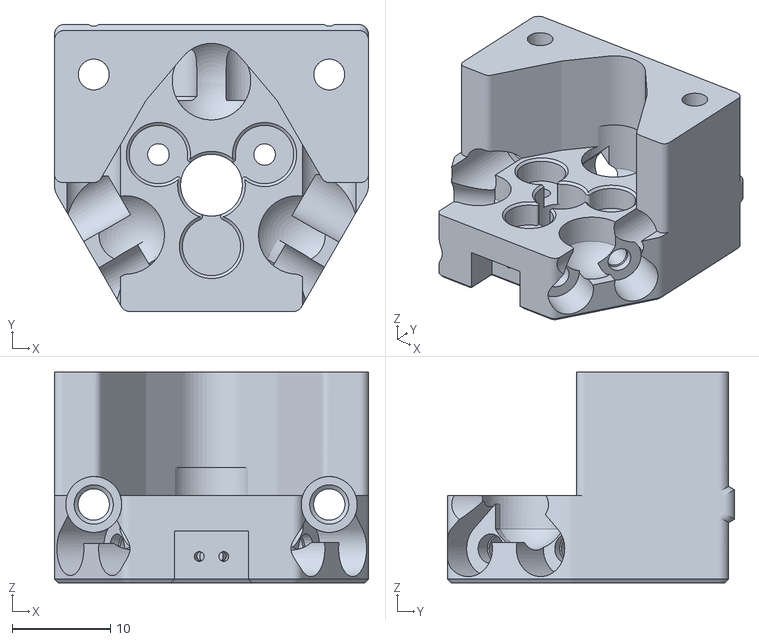
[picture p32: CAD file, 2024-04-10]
STLs/nudge_1515_low.stl
32.0 x 29.2 x 21.5

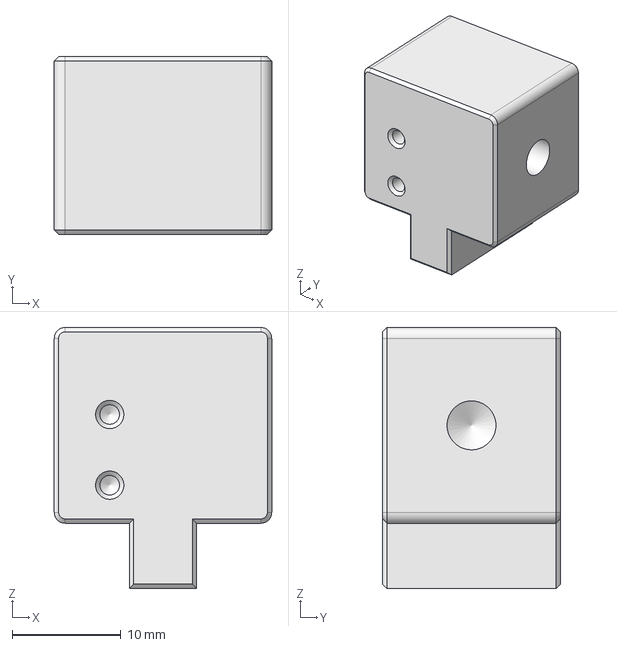
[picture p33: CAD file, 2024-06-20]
User Mods/VIN-y/Removable 2.4 Mount/CADs/Nudge_Mount Part 2.step
20.0 x 16.4 x 24.0 mm

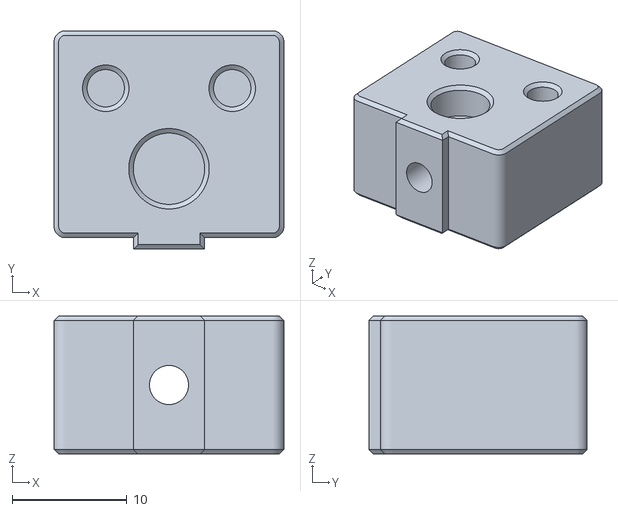
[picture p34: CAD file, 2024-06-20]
User Mods/VIN-y/Removable 2.4 Mount/STLs/Mount Dock x2.stl
20.0 x 19.0 x 12.0

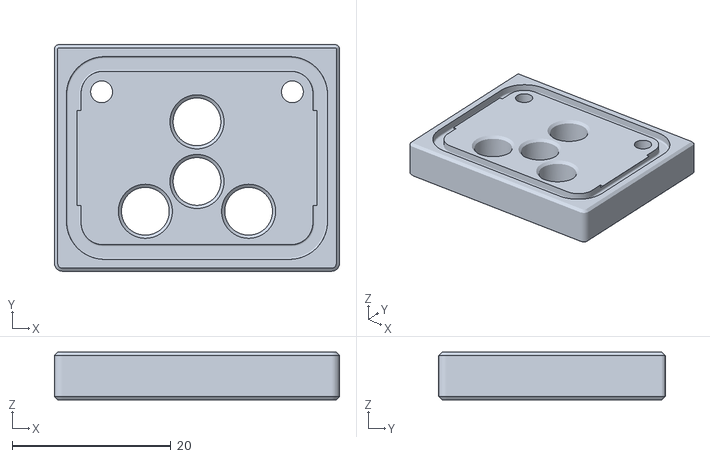
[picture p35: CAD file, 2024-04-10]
STLs/base_floating.stl
35.8 x 28.5 x 6.00

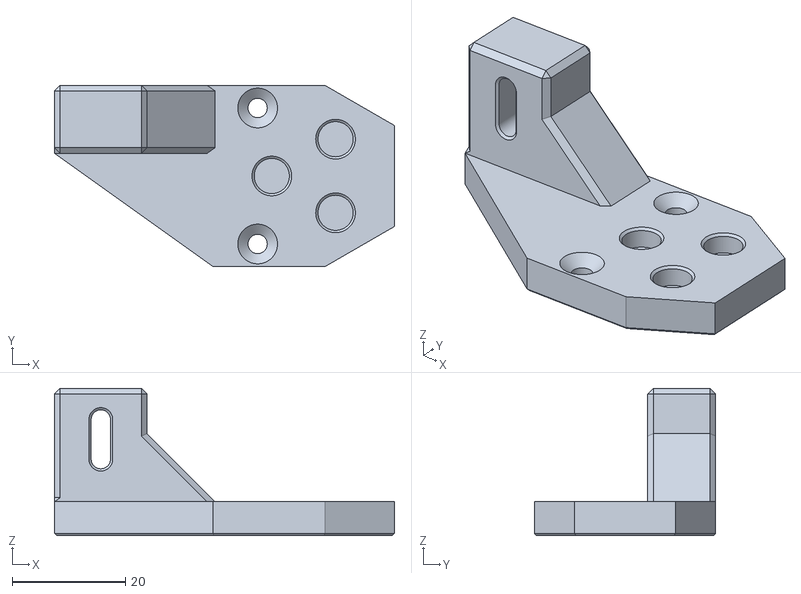
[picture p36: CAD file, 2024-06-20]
User Mods/VIN-y/Removable 2.4 Mount/STLs/Nudge_Mount Part 1.stl
60.0 x 32.0 x 26.0

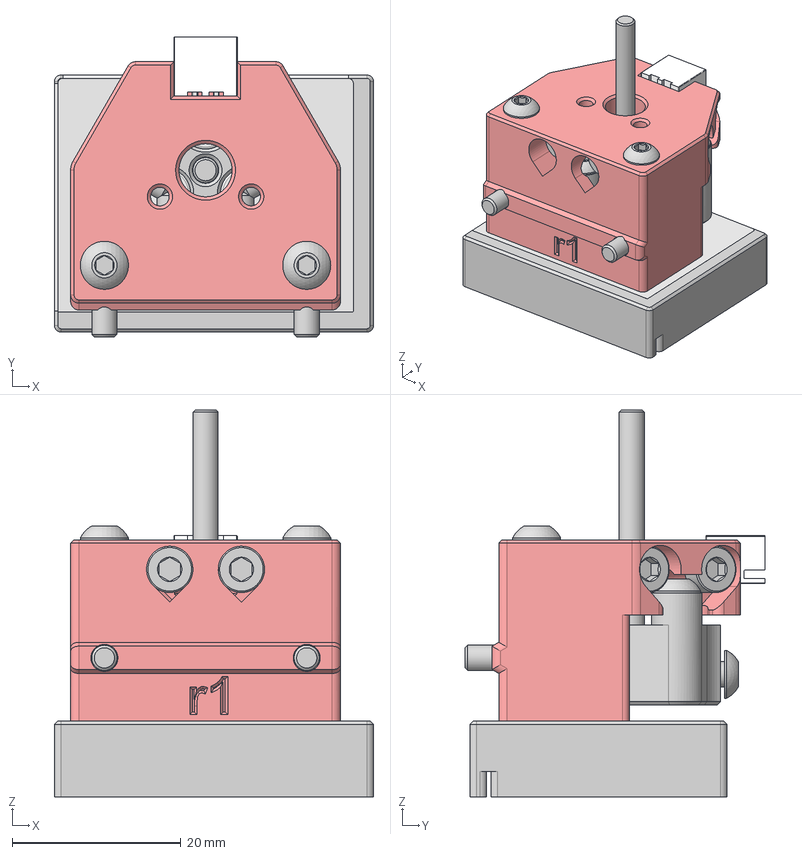
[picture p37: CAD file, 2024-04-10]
CAD/Nudge_All_Bases.step
37.8 x 35.6 x 45.9 mm
M3x6 SHCS x 6
6x3mm Magnet x 6
Floating Base
Indexed Base
M3x25 BHCS v1 x 2
Adjustable Dowel
SHCS
m3_pin_main 35mm
M3_Hexnut
M3x10 BHCS v1
M3x6 BHCS v1 x 3
XH2.54-2P
M3x12 SHCS v1 x 2

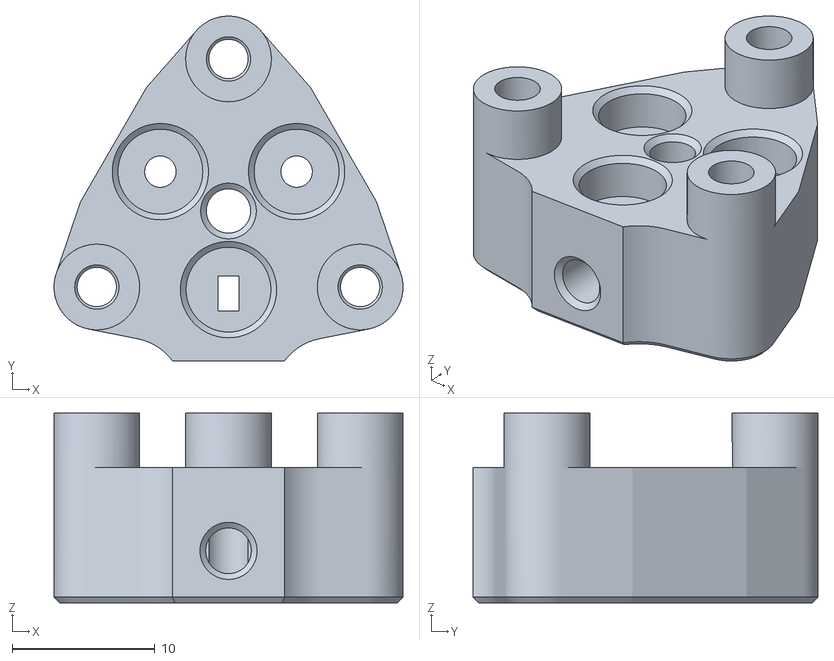
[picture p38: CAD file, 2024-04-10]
STLs/wobbler_3mm.stl
24.4 x 24.2 x 13.3

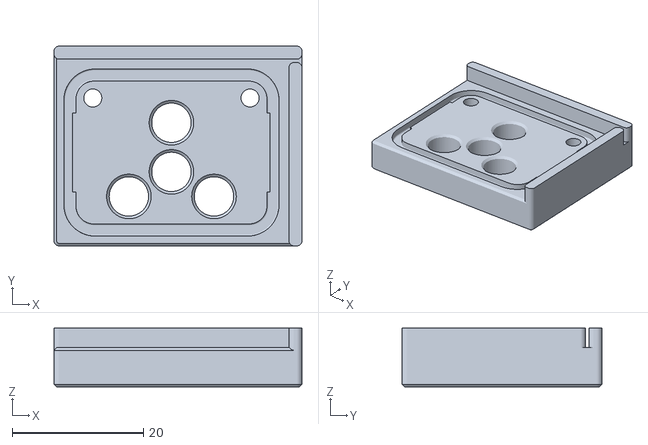
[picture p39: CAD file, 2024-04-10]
STLs/base_indexed.stl
37.8 x 30.5 x 9.00

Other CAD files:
CAD/Nudge_2020_5mm.step
User Mods/VIN-y/Removable 2.4 Mount/CADs/Mount Dock x2.step
User Mods/VIN-y/Removable 2.4 Mount/CADs/Nudge_Mount Part 1.step
User Mods/VIN-y/Removable 2.4 Mount/STLs/Nudge_Mount Part 2.stl
CAD/Nudge_1515_Low_3mm.step
STLs/nudge_2020.stl
STLs/wobbler_5mm.stl
STLs/nudge_1515_high.stl
CAD/Nudge_1515_High_3mm.f3z
CAD/Nudge_1515_Low_3mm.f3z
CAD/Nudge_2020_5mm.f3z
CAD/Nudge_All_Bases.f3z
CAD/Nudge_v68_Configured.f3z

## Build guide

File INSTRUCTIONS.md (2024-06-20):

### Step 0: Fetch tools

Required:
* Allen drivers for M3 BHCS and SHCS - straight (non-ball-type) preferred

Recommended:
* Multimeter
* 3mm drill bit or (preferred) 3mm reamer

### Step 1: Choose mount type, wobbler type, and probe target length

Nudge comes in a variety of options, to fit any printer.

The key to the choice is the amount of overtravel: **overtravel** is the amount of travel beyond the edge of the bed, in X or Y, and it drives the mount and wobbler choice.

| No overtravel available... <br>and no way to add it? <br>(most moving-bed printers) | At least 6mm overtravel already available | Less than 6mm overtravel |
| --- | --- | --- |
| Use floating mount or indexed mount | Use Nudge mount by itself | Add overtravel (typically by shifting the bed forward) then use Nudge mount <br><br> OR <br><br> Make a custom detachable mount |

#### Choose mount type

First, choose the mount type for your printer.  Note:
* The location of the probe tip must be available to *all* heads; on some IDEXes (especially bed-flingers and cantilevered-bed printers like the V0), this can be a challenge.
* If using the floating or indexed mount option, go with the 2020 core type.
* If mounting to an extrusion, make a choice based on the printer type; see examples at the bottom of the table below.

| 2020 | 1515 High | 1515 Low |
| --- | --- | --- |
|  |   |  |
| Aligned to bottom of 2020 extrusion | Aligned to bottom of 1515 extrusion | Aligned to top of 1515 extrusion |
| Trident, Tridex, V2 | F-Zero, Micron | Tri-Zero, Pandora/Pandora's Box |

#### Choose wobbler type

The wobbler come in two sizes, with tight 3mm or 5mm slip-fit holes.

If you have 6-8mm of available overtravel, you’ll want the narrowest probe target choice: an M3 pin.

Beyond 8mm of available overtravel, any target choice will work fine.  

M3 or M5 pins are preferred for ease of sourcing and ease of adjustment.  

However, many other choices will work just fine, too, if you have them handy.

**Shown below**: M3 Pin, M5 Pin, M3 BHCS with nut and internally-threaded dowel:


An FHCS would probably work fine too.  The key is to have a flat upper surface for Z probing.

#### Choose probe target length

**It depends.**  Wait...depends on what?  Depends on bed-mount details (spacer height, bed height, extrusion height, magsheet?), overtravel, mount type, and wobbler type.  *That's a lot*, so it's best to determine the height empirically.

Generally, a longer pin is better as it reduces the forces experienced on the nozzle, which reduces belt stretch effects.

For floating and indexed mounts, anything 35mm+ should be fine.

For fixed mounts, the ideal position for the top of the probe target is about 1mm above the print surface, to provide space to trigger from XY motion, but low enough to not catch on the toolhead as it moves near the edge of the bed.

To find the ideal length for the probe target, measure from the top of the bed flexplate to the bottom of the mount (bottom of mounting extrusion with 2020 and 1515 high, and ~6mm below extrusion on 1515 low). The 1mm stick-out is roughly matched by the little bit of of clearance to the bottom of the wobbler.  Round up to the next available size (typically a 5mm increment).

If you buy a slightly-too-long pin, it can be chopped, or ignored, if you don't intend to completely max out your Z travel.

### Step 2: Buy non-printed parts

See the [BOM](BOM.md) for details on the other stuff to buy, which you probably already have handy - screws, nuts, magnets - plus the M3x6 smooth copper SHCS that you probably don't have.

### Step 3: Print the printed bits

For all Nudge parts, use standard Voron settings: 40% infill, 4 perims, 0.4 width, 5 top/bottom layers.

Use ABS or other temp-resistant material, if it will be rigidly mounted near the bed.

You want a well-calibrated printer to get glueless magnet insertions and for best accuracy.

### Step 4: Assemble and test

See this video for the build:

(https://youtu.be/6eRomxUo7TI)

The video should give a good sense of what's involved, plus show some assembly tricks, but it's slightly out of date - for example, now, Nudge has a straight-through JST, rather than a right-angle JST.

I know, I know, it looks a bit long for a two-part assembly, but there's a lot going on here, and if you're aggressive with the formed threads, you may have to reprint the mount.  

So - read up, then go to town.  The order below is actually the recommended assembly order now.

#### Learn proper formed-thread tightening!
*If you overtorque a screw, you’ll have to reprint the base part.*  Nobody wants that.

Each formed-thread hole has an “easy start” (Zruncho's term) - a small clearance-size counterbore to help align the screw.  You push in to the easy start, until you get to the hole chamfer.  The screw holds itself in place.

Then, to make a good formed thread, push hard with an allen driver.  Keep turning it until you feel a bit of resistance, looking at whether the screw head is hitting anything.

To prevent stripping the formed threads, DON’T use the long side of an allen wrench; use the short end or pinch the smallest section of a driver handle.

#### Do the build

* Find a 2-pin JST-XH plug for use when adding the pins
* Prep printed parts
  * Gently clear the central wobbler hole for the pin, using a drill bit or reamer
  * Gently clear the retention-screw hole in the wobbler
* Install Magnets
 * Set your convention with a different magnet/alloy screw/mark on the stack.
 * Wobbler
   * Push down hard with fingers or against a flat surface; a magnet should push into place, securely, without glue.
   * Repeat for all 3 magnets
 * Mount
   * FLIP THE MAGNET DIRECTION!
   * Same thing; push hard
   * Repeat for all 3 magnets
 * Test that the two parts mate.  If you got the direction wrong, use the access holes in the wobbler, along with a tiny allen key, to evict the magnets and try again.
* Build wobbler
 * Push an M3x6 BHCS into the easy start
 * Form threads until fully tightened
 * Repeat for all 3 BHCS
 * Push retention-screw nut fully into bottom of wobbler
 * Insert and slightly tighten retention screw (but not enough to block insertion of the probe)
 * Add probe target (pin or screw); note that the 5mm pin will be tight with the magnets, so if adjusting the pin upwards, hold the magnets in place, or push them back down afterwards.
* Build mount
 * Push SHCSes until they hold in place and tighten a few turns
 * Add terminal plug to JST
 * Push JST fully into mount; yes, it will stick out above slightly
 * Push hard on the JST plug + terminal; keep holding as you tighten the two relevant screws.
 * Tighten 2 front SHCSes until they're fully inserted; go slow, as these screws will try to push out the square JST terminals. The screws are positioned to cut grooves into the terminals.
 * Test that the JST terminal resists some pull-out force: plug pullout/reinsert a few times.
 * Flip the core to its belly, so you can see the screw threads
 * Fully tighten rearmost 2 screws
 * Fully tighten middle two screws; look into the viewing holes to see the screw tips hit.  Don't overtighten.  You just need electrical contact and a bit of force to preload.  Keep going and it'll strip.
* Assemble
 * Put wobbler into mount and test for “clickiness”.
 * Play with it!  You have a killer fidget toy now.
* Initial Electrical test
 * Use a multimeter to confirm end-to-end continuity between JST terminals
   * If using steel screws, you should expect some resistance; up to a few hundreds ohms is OK
   * If using copper, expect single-digit or less ohms.
 * If you see no reading, make sure you have a higher (2K) ohms setting on the multimeter first.
   * Then, test each pair of neighboring screws in place to identify the issue.  If no continuity, then further tighten the relevant screws
   * Still not working?  
     * Ensure flat print
     * Ensure screws aren’t crap (heads are actually cylindrical)
     * Clean screws and ensure they’re actually conductive
     * Ensure magnets don’t have wrong polarity
* Optional for bases
 * Trim TPU to desired length
 * Push in base magnets, keeping same orientation
 * Screw in two 2x M3x25 BHCS; these are intentionally tight holes.
* Test-mount to confirm the probe type and length are about right; you can adjust slightly in place.

#### Basic electrical checkout

Here's a cool way to test the probe in Klipper, as a "filament sensor".

Add this to your `printer.cfg`, and make sure to update the pins.
```
[duplicate_pin_override]
pins: head1:PB12

[filament_switch_sensor head1_attached]
switch_pin: head1:PB12
pause_on_runout: false
```

Restart Klipper.

In your web interface for Klipper, look at the filament value; at least with Mainsail, it'll update automatically!  Tap the probe with your finger to knock it off-position slightly; the value should change.  Then have it return to center and ensure that it registers nothing.  Do this 5 times to be sure.

Switch back to the original port if needed.

Congrats!  Your probe appears to work.

#### Install in printer

This one's on you.

#### Configure software and test functionality

Move on to the [Configuration](CONFIGURATION.md) section!

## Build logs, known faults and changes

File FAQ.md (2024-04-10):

## FAQ

### Why does this exist?

It’s pretty simple: **All calibration is toil.  It’s wasted effort.**

The more knowledge someone needs to add a second toolhead to their printer... the fewer people will try adding that second toolhead.  And if you’re gonna add automatic calibration, it shouldn’t require work either.  It should run automatically before every print, just like bed leveling, so no matter the change, you get perfect alignment.

Because calibration represents work, Double Dragon has been idle for 2 yrs and Dueling Zero has never had a non-calibration two-head print.  They've been waiting for something like this.

You don’t NEED automatic offset calibration, but we can do better.

It’s time to make multi-toolhead setups mainstream, and this is one of the keys.  Auto offset calibration is up there with firmware support, example macros, slicer support, and validated hardware designs.

### Why no servo-deployed version?

Extra cost, unnecessary, potential point of failure, and configuration complexity.

Feel free to make it, especially to support printers with no overtravel - but make sure to quantify the repeatability.  

### Why use formed threads here, vs heatsets?

In this application, they reduce the needed XY space, which helps fit inside a bedframe with smaller builds (especially Tri-Zero with Double Dragon).

Heatsets require some skill to align, add to the BOM, slow down the build, and would compromise midpiece packaging.  For applications where screws are unlikely to ever be retightened, like a probe, they make sense.

The key phrase is *in this application*.  Yes, formed threads can strip - if you’re a gorilla, or if the holes are too big.

### Isn't this all dependent on perfectly drilled nozzles?

Sure, it's true that the touch-probe-against-nozzle approach works best when the center of the nozzle hole aligns to the rest of the nozzle.  Otherwise, you'll get a consistent error.

Unless you're using super-cheap nozzles, that shouldn't be the case, though.

It is possible that the nozzle-drilling error outweights the error introduced from the touch probe, but this would need some testing against another calibration system, such as a vision-based one.  Speaking of which...

### Why not [X] for probe alignment?

Other choices may work fine for you, and perform identically; the real differentiators here are the “batteries-included” mounting options, high level of quantified testing, and minimized required overtravel.

Compared to Viesturz' NozzleAlign probe (linear rail with target), the Z height is much faster and easier to adjust in-situ with Nudge and it does not encroach into the build space.

Compared to Viesturz’ Ball Probe, the parts are all easily available and require no grinding or custom sourcing.

Compared to “NozzleAlign Lite” (a 2020 endstop with an M6 acorn nut glued on top), acorn nut alignment quality, long-term wear, and pin rotation creating error when combined with acorn nut to pin misalignment, and  are not concerns.

Compared to vision-based systems, there is no concern about long-term longevity in a heated chamber, or code installation and configuration, and the method is less sensitive to nozzle occlusion from crud.

### Do I really need copper screws?  I can’t find those.

Steel will work fine, but the connectivity will be slightly harder to test, and the resistance may vary each time it’s touched.  

Copper is easier to test and can use lower magnet forces as a result.

If you can't source the copper ones, try it with steel first.  In tests, it has worked fine, despite a higher measured resistance.

### Can I flip the Nudge if already have Tap and don’t want two things moving during probing?

**Yes!**  There are two ways to mount Nudge.  Normal (XYZ) mode and flipped (XY-only) mode.  In XY-only mode, you need something Tap-like.  This isn't advertised on the main page, just to reduce

* XYZ Probe - can be pushed downwards, and serve as a Z target.  Requires a probe target with a flat top - a pin, FHCS, or internally-threaded dowel.  Use with any non-moving-toolhead printer.

* XY Probe - so named because you can’t do Z calibration with it.  It won’t move downwards.  For this option, the mount is simply flipped.  The target then becomes a shorter length.  Benefit: can use more choices of target, such as a SHCS or BHCS, and possibly better Z probing with moving-nozzle Z probes (Tap, Boop, Poke, etc).

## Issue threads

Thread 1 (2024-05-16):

probe triggered prior to movement

seene, 2024-05-16:
Hey,

unfortunately I have a problem determining the nozzle position

Z works normally, but as soon as the nozzle triggers on X axis, I get the following error message: “probe triggered prior to movement”

I am using an Idex printer with Hybrid CoreXY w/ Dual Carriage.  I have already installed “Frans-Willem's Klipper PR”.
I have also tried the troubleshooting of “viesturz/NozzleAlign” without success.

do you have any idea what could be causing this?

seacred, 2024-06-16:
i got the same issue unfortunately.

TTom1088, 2024-06-17:
i got the same issue. I've tried many different options. I suspect there is a problem in the software, as everything is fine in terms of hardware.

VIN-y, 2024-06-17:
Alright. Since it seems like this issue is being discuss more over here. I will move this comment here.

Nothing really came to my mind of what could have cause you issue. So, let's try breaking this down further.

There are 4 components to the calibration probe: hardware assembly, electrical wiring, the .cfg file, and the underlying python code.

You said Z works normally. So I am assuming that, after initiated, the machine would pick up T0 and move to calibration probe pin position. Then it moved down until it triggered the probe. Then it starts the x measurement, which is where the error occur? --- If so. We can push the hardware-assembly and electrical-wiring to the back of the potential-problem queue for now. The next thing to go over is your calibrate-offsets.cfg file. That is not to say that the config is the problem, as it is just a list of numbers for your tool-head to move along.

Follow the logic above, maybe you the tip of your hotend touched the pin when it moving toward the starting position for the x calibration, which then trigger the error for safety.

So... what hotend are you using? can we see your config file? and, can you check on for the potential cause above?

TTom1088, 2024-06-17:
I have now analyzed the problem further. I use an IDEX hybrid core xy. Z works perfectly. But as soon as X is connected, the error message "probe triggered prior to movement" appears. But only when the nozzle "triggers" the probe; manual triggering during X reversing also generates this error.

Since Z always works, I suspect there is a software error in the program. The problem is probably because the nudge switches an NC contact. The switch from viesturz uses NO logic and the problem probably does not occur there.

TTom1088, 2024-06-20:
I have now found a solution for this online. It is a software error that only affects IDEX printers, here is the solution:

https://github.com/viesturz/klipper-toolchanger/pull/23/commits/3f7e2c1dc7e5ceac8e3972c9b5906ef8c089aa3e

seene, 2024-06-20:
yes, I forgot to update the issue.
With the latest version of klipper-toolchanger there should be no more problems.

I will close the issue now

Closed 2024-06-20.

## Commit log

2024-04-10 Closed beta release
    [base_floating.stl, base_indexed.stl, nudge_1515_high.stl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]
2024-04-10 Add CAD exports
    [Nudge_1515_High_3mm.f3z, Nudge_1515_High_3mm.step, Nudge_1515_Low_3mm.f3z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]
2024-04-11 Fix alignment in BOM
2024-06-05 Add user mod
    VIN-y. Removable mounting option for Voron 2.4.
    [Mount Dock x2.step, Mount Dock x2.stl, Nudge_Mount Part 1.step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]
2024-06-20 Major doc update
    Note move for Viesturz' code
    Add troubleshooting notes
    Add sample video
    Note IDEX support from RCF patch
2024-06-21 Bugfix to macro: set temp of active extruder
    Thanks SteveBuilds for the fix
